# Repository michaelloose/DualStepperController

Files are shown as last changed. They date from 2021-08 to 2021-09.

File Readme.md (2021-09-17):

Stepper Controller
==================

Dieses Projekt entstand als kleines Nebenprojekt im Rahmen meiner Masterarbeit und soll eine performante und einfach anzusteuernde Möglichkeit bieten zwei Schrittmotoren mithilfe eines Schrittmotortreibers wie dem DM542 zu betreiben.

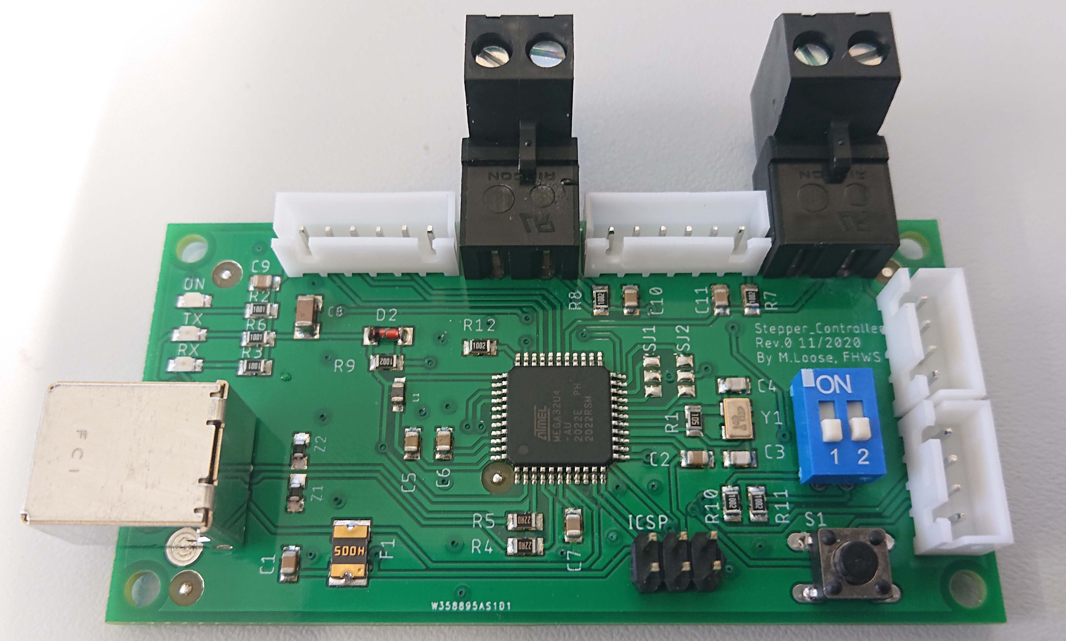
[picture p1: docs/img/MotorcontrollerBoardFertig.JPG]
Platine
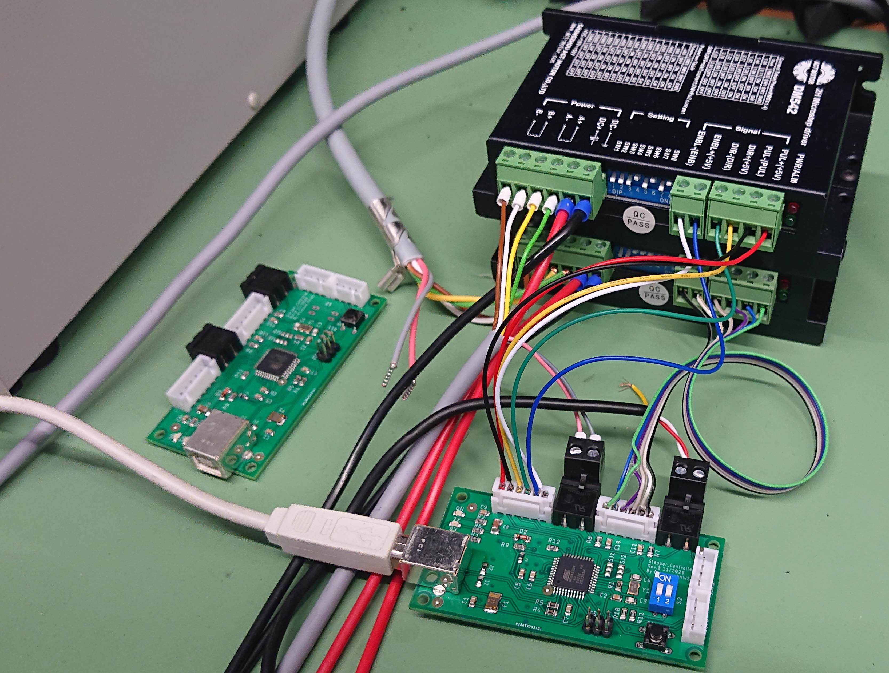
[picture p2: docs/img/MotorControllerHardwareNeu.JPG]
Beispielaufbau
||
|:---:|:---:
|Bestückte Leiterplatte |Beispielhafter Aufbau 

## Befehlsübersicht

Die Übertragung findet
über einen mittels USB-CDC emulierten COM-Port statt. Aus diesem
Grund sind sämtliche Einstellungen zu Baudrate, Daten/Stopbits oder
Paritätsbits hinfällig. Der Controller unterscheidet bei den Befehlen
nicht zwischen Groß- und Kleinschreibung. Das Ende eines Befehles wird
durch ein Carriage Return `<CR> Hex:0x0D` signalisiert. Alternativ wird
auch ein Line Feed `<LF> Hex:0x0A` akzeptiert. Ein Befehl darf eine
maximale Länge von zwölf ASCII-Zeichen zuzüglich des Terminatorzeichens
aufweisen. Wird diese Länge überschritten, so wird das dreizehnte
Zeichen unabhängig vom Inhalt aus Terminator gewertet.\
Zum Testen des Controllers wird eine serielle Konsole benötigt. Dazu
eignet sich die Software *hTerm*, welche sowohl unter Windows
als auch unter Linux ausgeführt werden kann. Um den Motortreiber in eine
Softwareumgebung einzubinden, wurde eine
Treiberklasse in Python entwickelt, die es einem ermöglicht
Steuerbefehle auf einem hohen Level zu senden. Zusätzlich zu dieser
Treiberklasse existiert ebenfalls eine GUI um die Antriebe komfortabel manuell
verfahren zu können.

### Allgemeine Befehle

  |Name               |Befehl     |Erklärung
  |-------------------|-----------|-----------------------------------------------------------------------------------------------------------------------------------------------------
  |Reset              |`RST<cr>`  |Neustart des Controllers. Trennt ebenfalls die USB-Verbindung.
  |Halt               |`HLT<cr>`  |Anhalten aller Antriebe. Neue Befehle werden akzeptiert, Spulen sind weiterhin bestromt.
  |Not-Halt           |`EST<cr>`  |Anhalten aller Antriebe. Neue Befehle werden nicht mehr akzeptiert, Spulenstrom wird abgeschaltet, somit können die Antriebe von Hand bewegt werden
  |Freigabe Not-Halt  |`ESR<cr>`  |Rücksetzen des Not-Halt Zustandes. Spulenstrom wird aktiviert und neue Befehle akzeptiert.

### Steuerbefehle

#### Steuerbefehle an den Controller
 | Byte    |Erlaubte Werte                                | Erklärung
 | ------- |----------------------------------------------| -------------------------------------------------
 | 1       |`A` Antrieb A (Hier Drehtisch)                | Antrieb
 |         |`B` Antrieb B (Hier Linearantrieb)            | 
 | 2       |`P` Position                                  | Art des Befehls
 |         |`S` Geschwindigkeit                           | 
 |         |`H` Anhalten (Setzt Sollwert gleich Istwert)  | 
 |         |`Z` Soll- und Istwert auf 0 setzen            | 
 |         |`R` Referenzfahrt                             | 
 | 3       |`=` Zuweisung                                 | Zuweisung oder Abfrage
 |         |`?` Abfrage                                   | 
 | 4\...   |`<Wert>` Punkt als Dezimalseparator           | Nur für Setzen von Position und Geschwindigkeit
 | N       |`<CR>` Carriage Return                        | Ende eines Befehls

#### Antwort vom Controller

  |Byte   |Erlaubte Werte                             |Erklärung
  |-------|-------------------------------------------|-------------------------------------
  |1..2   |Byte 1 u. 2 des Befehls                    |Wiederholen des empfangenen Befehls
  |3      |`!` Ausführung Abgeschlossen               |Art der Antwort
  |       |`=` Befehl Empfangen, Antwort auf Anfrage  |
  |4\...  |`<Wert>` Punkt als Dezimalseparator        |Wert als Antwort einer Anfrage
  |N      |`<CR>` Carriage Return                     |Ende eines Befehls

### Parametrierbefehle

Um den Controller zu parametrieren muss dieser zunächst mittels des
Befehls `PARAM` in den Parametriermodus gebracht werden. Der Controller
quittiert diesen Modus mit der Ausgabe `PARAM`. In diesem Modus können
die Antriebe nicht verfahren werden. Wird dennoch ein Verfahrbefehl
gesendet, so wird dieser nicht ausgeführt und der Controller antwortet
wie bei einem ungültigen Befehl mit `?`. Der Parametriermodus kann mit
dem Befehl `EXIT` wieder beendet werden. Das Verlassen der
Parametriermodus wird vom Controller mit `OK` Quittiert. Der Controller antwortet auf
Parametrierbefehle in der selben Weise wie auf Steuerbefehle.\

  |Byte    |Erlaubte Werte                          | Erklärung
  |--------|----------------------------------------| ------------------------------------
  |1       |`A` Antrieb A                           | Antrieb
  |        |`B` Antrieb B                           |
  |2\...4  |`SPU`                                   | Schritte pro Einheit
  |        |`VLM`                                   | Geschwindigkeitsbegrenzung \[1,0\]
  |        |`VMX`                                   | Maximale Geschwindigkeit
  |        |`VDF`                                   | Standardgeschwindigkeit
  |        |`PLM`                                   | Positionssbegrenzung \[1,0\]
  |        |`PMX`                                   | Maximale Position
  |        |`PMN`                                   | Minimale Position
  |        |`ROF`                                   | Offset vom Referenzpunkt
  |        |`DIN`                                   | Richtungsumkehrung \[1,0\]
  |        |`RPL`                                   | Polarität Referenzschalter \[1,0\]
  |        |                                        | 0: Öffner, 1: Schließer
  |5       |`=` Zuweisung                           | Zuweisung oder Abfrage
  |        |`?` Abfrage                             | 
  |6\...   |**\<Wert>** Punkt als Dezimalseparator  | 
  |N       |**\<CR>** Carriage Return               | Ende eines Befehls

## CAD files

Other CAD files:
PCB/Partslist.prt

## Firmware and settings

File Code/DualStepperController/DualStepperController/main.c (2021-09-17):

/*
* main.c
*
* Created: 6/11/2021 10:40:07 AM
*  Author: Waxrek
*/
#include "headers.h"





static RingBuffer_t RxBuffer;
static uint8_t RxBufferData[RX_BUFFER_LEN];


/** LUFA CDC Class driver interface configuration and state information. This structure is
*  passed to all CDC Class driver functions, so that multiple instances of the same class
*  within a device can be differentiated from one another.
*/
USB_ClassInfo_CDC_Device_t VirtualSerial_CDC_Interface =
{
	.Config =
	{
		.ControlInterfaceNumber   = INTERFACE_ID_CDC_CCI,
		.DataINEndpoint           =
		{
			.Address          = CDC_TX_EPADDR,
			.Size             = CDC_TXRX_EPSIZE,
			.Banks            = 1,
		},
		.DataOUTEndpoint =
		{
			.Address          = CDC_RX_EPADDR,
			.Size             = CDC_TXRX_EPSIZE,
			.Banks            = 1,
		},
		.NotificationEndpoint =
		{
			.Address          = CDC_NOTIFICATION_EPADDR,
			.Size             = CDC_NOTIFICATION_EPSIZE,
			.Banks            = 1,
		},
	},
};



int main (void) {


	testCounter = 0;
	driveState = DRV_STATE_RDY;
	
	/* Disable watchdog if enabled by bootloader/fuses */
	MCUSR &= ~(1 << WDRF);
	wdt_disable();
	
	/* Disable clock division */
	clock_prescale_set(clock_div_1);
	USB_Init();

	sei();
	
	
	DDRB |= (1 << 0);
	DDRD |= (1 << 5);
	
	PORTB |= (1<<0);    //Bit setzen, LED AUS
	PORTD |= (1<<5);    //Bit setzen, LED AUS
	//PORTD &= ~(1<<5);    //Bit setzen, LED AN
	
	// Initialize the buffer with the created storage array
	RingBuffer_InitBuffer(&RxBuffer, RxBufferData, RX_BUFFER_LEN);
	
	stepper_a_init();
	stepper_b_init();

	while(1){

		/*
		testCounter++;
		
		if(testCounter > 20000){
			testCounter = 0;
			PORTB |= (1<<0);    //Bit setzen, LED AUS
			PORTD &= ~(1<<5);    //Bit loeschen, LED AN
		}
		
		else if(testCounter > 10000){
			// halbe sekunde warten
			PORTB &= ~(1<<0);   // Bit loeschen, LED AN
			PORTD |= (1<<5);    //Bit setzen, LED AUS
		}
		//fputs((char*)&testCounter, &USBSerialStream);
		*/
		
		
		stepper_a_loop(&VirtualSerial_CDC_Interface);
		stepper_b_loop(&VirtualSerial_CDC_Interface);

		putCDCtoBuffer(&VirtualSerial_CDC_Interface, &RxBuffer);
		checkBufferForCommands(&VirtualSerial_CDC_Interface, &RxBuffer);
		
		/*
		if(commandState == CMD_STATE_RDY_TO_EXEC){
			pCommandBuffer = commandBuffer;
			char nextChar = *pCommandBuffer++;
			
			while(nextChar != 0x00){
				CDC_Device_SendByte(&VirtualSerial_CDC_Interface, nextChar);
				nextChar = *pCommandBuffer++;
			}
			commandState = CMD_STATE_EXECUTED;
		}
		*/
		
		handleCommands(&VirtualSerial_CDC_Interface);
		CDC_Device_USBTask(&VirtualSerial_CDC_Interface);
		USB_USBTask();
	}
	
	return 0;
}






/** Event handler for the library USB Connection event. */
void EVENT_USB_Device_Connect(void)
{
	//LEDs_SetAllLEDs(LEDMASK_USB_ENUMERATING);
}

/** Event handler for the library USB Disconnection event. */
void EVENT_USB_Device_Disconnect(void)
{
	//LEDs_SetAllLEDs(LEDMASK_USB_NOTREADY);
}

/** Event handler for the library USB Configuration Changed event. */
void EVENT_USB_Device_ConfigurationChanged(void)
{
	bool ConfigSuccess = true;

	ConfigSuccess &= CDC_Device_ConfigureEndpoints(&VirtualSerial_CDC_Interface);

	//LEDs_SetAllLEDs(ConfigSuccess ? LEDMASK_USB_READY : LEDMASK_USB_ERROR);
}


/** Event handler for the library USB Control Request reception event. */
void EVENT_USB_Device_ControlRequest(void)
{
	CDC_Device_ProcessControlRequest(&VirtualSerial_CDC_Interface);
}

/** CDC class driver callback function the processing of changes to the virtual
*  control lines sent from the host..
*
*  \param[in] CDCInterfaceInfo  Pointer to the CDC class interface configuration structure being referenced
*/
void EVENT_CDC_Device_ControLineStateChanged(USB_ClassInfo_CDC_Device_t *const CDCInterfaceInfo)
{
	/* You can get changes to the virtual CDC lines in this callback; a common
	use-case is to use the Data Terminal Ready (DTR) flag to enable and
	disable CDC communications in your application when set to avoid the
	application blocking while waiting for a host to become ready and read
	in the pending data from the USB endpoints.
	*/
	//bool HostReady = (CDCInterfaceInfo->State.ControlLineStates.HostToDevice & CDC_CONTROL_LINE_OUT_DTR) != 0;
}

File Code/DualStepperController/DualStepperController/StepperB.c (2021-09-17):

/*
* StepperA.c
*
* Created: 05.07.2021 11:06:45
*  Author: Waxrek
*/
//#include "StepperB.h"
#include "headers.h"



void stepper_b_init(){
	
	
	eeprom_read_block(&stepper_b_settings, (void*)STEPPER_B_SETTINGS_START_ADDR, sizeof(stepper_b_settings));
	stepper_b_moving = 0;
	stepper_b_direction = 0;
	stepper_b_hasPreviouslyMoved = 0;
	stepper_b_hasPreviouslyHomed = 0;
	stepper_b_referencing = 0;
	stepper_a_prescalerFactor = 0;
	stepper_b_setpoint = 0;
	stepper_b_position = 0;

	
	
	//Ausgänge definieren
	STEPPER_B_STEP_DDR |= (1 << STEPPER_B_STEP_N);
	STEPPER_B_DIRECTION_DDR |= (1 << STEPPER_B_DIRECTION_N);
	STEPPER_B_ENABLE_DDR |= (1 << STEPPER_B_ENABLE_N);
	//Eingang definieren
	STEPPER_B_REFERENCE_DDR &= ~(1 << STEPPER_B_REFERENCE_N);
	
	//Enable auf HIGH setzen
	STEPPER_B_ENABLE_PORT &= ~(1<<STEPPER_B_ENABLE_N);
	
	//Register fuer Timer setzen
	//Interrupts deaktivieren
	cli();
	// Register mit 0 initialisieren

	STEPPER_B_TIMER_TCCRA = 0b00000000; //Register für PWM
	STEPPER_B_TIMER_TCCRB = 0b00011000;//Register für Prescaler: //WGM12 setzen, WGM13 setzen. Aus Irgend einem Grund Behebt das Setzen von WGM13 das Problem, dass nur das Low Byte vom OCRA Register beschrieben wird
	STEPPER_B_TIMER_TCNT = 0b00000000; //Counter Register
	STEPPER_B_TIMER_TIMSK = 0b00000010;

	sei();
	stepper_b_setSpeed(stepper_b_settings.speed_default);
}


void stepper_b_loop(USB_ClassInfo_CDC_Device_t* pInterface){
// 	if (stepper_b_settings.polarity_reference_switch != ((STEPPER_B_REFERENCE_PIN & (1 << STEPPER_B_REFERENCE_N)) == (1 << STEPPER_B_REFERENCE_N)))
// 	PORTD &= ~(1<<5);    //Bit setzen, LED AN
// 	else
// 	PORTD |= (1<<5);    //Bit setzen, LED AUS
	
	//In welchem Zustand befindet sich der Referenzierungsvorgang?
	switch (stepper_b_referencing)
	{
		case 1:
		//Antrieb bei aufgerufener Referenzierung ausserhalb des Fangbereiches des Endschalters
		
		//Überprüfe ob Istwert = Sollwert
		if(stepper_b_position != stepper_b_setpoint){
			stepper_b_setMotionState((stepper_b_position < stepper_b_setpoint)? 1: -1);
		}
		else{
			stepper_b_setMotionState(0);
			stepper_b_referencing = 0;
		}


		break;
		
		case 2:
		//Antrieb bei aufgerufener Referenzierung ausserhalb des Fangbereiches des Endschalters
		if (stepper_b_settings.polarity_reference_switch != ((STEPPER_B_REFERENCE_PIN & (1 << STEPPER_B_REFERENCE_N)) == (1 << STEPPER_B_REFERENCE_N)))
		{
			
			stepper_b_referencing = 1;

			stepper_b_position = stepper_b_settings.reference_offset * stepper_b_settings.steps_per_unit;
			stepper_b_setpoint = 0;
			
		}
		else
		{
			stepper_b_setMotionState(-1);
		}
		break;

		case 3:
		//Befand sich der antrieb bei aufgerufener Referenzierung im Fangbereich des Endschalters?
		//Ist der Endschalter noch aktiv?
		if (stepper_b_settings.polarity_reference_switch != ((STEPPER_B_REFERENCE_PIN & (1 << STEPPER_B_REFERENCE_N)) == (1 << STEPPER_B_REFERENCE_N)))
		{
			stepper_b_setMotionState(1);
		}
		else
		{
			stepper_b_setMotionState(0);
			stepper_b_referencing = 2;

		}
		break;

		default:
		//Überprüfe ob Istwert = Sollwert
		if(stepper_b_position != stepper_b_setpoint){
			stepper_b_setMotionState((stepper_b_position < stepper_b_setpoint)? 1: -1);
		}
		else{
			stepper_b_setMotionState(0);
		}
		break;
	}

	if ((stepper_b_moving == 0) && (stepper_b_hasPreviouslyMoved == 1))
	{
		

		if (stepper_b_hasPreviouslyHomed && !stepper_b_referencing)
		{
			stepper_b_hasPreviouslyMoved = 0;
			stepper_b_hasPreviouslyHomed = 0;
			CDC_Device_SendString(pInterface, "BR!\r");
		}
		else if(!stepper_b_hasPreviouslyHomed)
		{
			stepper_b_hasPreviouslyMoved = 0;
			CDC_Device_SendString(pInterface, "BP!\r");
		}
	}
	
}

void stepper_b_home(){
	stepper_b_hasPreviouslyMoved = 1;
	stepper_b_hasPreviouslyHomed = 1;

	if (stepper_b_settings.polarity_reference_switch != ((STEPPER_B_REFERENCE_PIN & (1 << STEPPER_B_REFERENCE_N)) == (1 << STEPPER_B_REFERENCE_N)))
	{
		//Status2: Antrieb befindet sich im Fangbereich des Endschalters
		stepper_b_referencing = 3;
		
		
		
	}

	else{
		//Status 1: Antrieb befindet sich nicht im Fangbereich des Endschalters
		stepper_b_referencing = 2;
		
	}
}
void stepper_b_zero(){
	stepper_b_setpoint = 0;
	stepper_b_position = 0;
}

void stepper_b_halt(){
	stepper_b_referencing = 0;
	stepper_b_setpoint = stepper_b_position;
}

uint8_t stepper_b_setSetPoint(double value){
	//Prüfen ob Wert in erlaubtem Bereich falls Positionsbegrenzung aktiviert
	if(stepper_b_settings.position_limit_enabled && ((value > stepper_b_settings.position_max)||(value < stepper_b_settings.position_min)))
	return 1;
	else
	{
		stepper_b_hasPreviouslyMoved = 1;
		stepper_b_setpoint = value * stepper_b_settings.steps_per_unit;
	}
	
	return 0;
}

double stepper_b_getPosition(){
	return (double)stepper_b_position / stepper_b_settings.steps_per_unit;
}


uint8_t stepper_b_setSpeed(double value){
	//Befehl nur akzeptieren wenn Wer
	if (value > 0 && ((value <= stepper_b_settings.speed_max)||stepper_b_settings.speed_max_enabled))
	{

		if ((value * stepper_b_settings.steps_per_unit) > 245)
		{
			//No Prescaler
			stepper_b_prescalerFactor = 1;
		}
		else if ((value * stepper_b_settings.steps_per_unit) > 31)
		{
			//Prescaler=8
			stepper_b_prescalerFactor = 8;
		}
		//Die Fälle ab hier sind eigentlich uninteressant, da sich das Teil eh nie so langsam bewegen wird, aber der Vollständigkeit halber nehm ichs mal auf
		else if ((value * stepper_b_settings.steps_per_unit) > 4)
		{
			//Prescaler=64
			stepper_b_prescalerFactor = 64;
		}
		else
		{
			//Prescaler=256
			stepper_b_prescalerFactor = 256;
		}

		stepper_b_speed_factor = (double)F_CPU / ((double)stepper_b_settings.steps_per_unit * (double)stepper_b_prescalerFactor);
		//Subtracting the Length of one Output Pulse (~2.9us per Step) in TimerRegister Units: Used to compensate the Length of the Pulse, so the Speed is accurate
		
		uint16_t ocr = (uint16_t)((stepper_b_speed_factor / value)-((double)PULSE_LEN * ((double)F_CPU / (double)stepper_b_prescalerFactor)));
		//uint16_t ocr = (uint16_t)(stepper_b_speed_factor / value);

		//_SFR_MEM16(OCRA) = (uint16_t)ocr;
		//Disable Interrupts
		cli();
		//_SFR_MEM8(OCRA+1) = (uint8_t)(ocr>>8);
		//_SFR_MEM8(OCRA) = (uint8_t)ocr;
		STEPPER_B_TIMER_TCNT = 0;
		STEPPER_B_TIMER_OCRA = ocr;
		//Enable Interrupts
		sei();

		return 0;
	}
	else
	{
		return 1;
	}
	
}
double stepper_b_getSpeed(){
	//return (stepper_b_speed_factor / (double)STEPPER_B_TIMER_OCRA);

	return (stepper_b_speed_factor/((double)STEPPER_B_TIMER_OCRA + ((double)PULSE_LEN * ((double)F_CPU / (double)stepper_b_prescalerFactor))));
}
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

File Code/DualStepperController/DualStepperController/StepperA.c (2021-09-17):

/*
* StepperA.c
*
* Created: 05.07.2021 11:06:45
*  Author: Waxrek
*/

#include "headers.h"



void stepper_a_init(){
	
	
	eeprom_read_block(&stepper_a_settings, (void*)STEPPER_A_SETTINGS_START_ADDR, sizeof(stepper_a_settings));
	stepper_a_moving = 0;
	stepper_a_direction = 0;
	stepper_a_hasPreviouslyMoved = 0;
	stepper_a_hasPreviouslyHomed = 0;
	stepper_a_referencing = 0;
	stepper_a_prescalerFactor = 0;
	stepper_a_setpoint = 0;
	stepper_a_position = 0;

	
	
	//Ausgänge definieren
	STEPPER_A_STEP_DDR |= (1 << STEPPER_A_STEP_N);
	STEPPER_A_DIRECTION_DDR |= (1 << STEPPER_A_DIRECTION_N);
	STEPPER_A_ENABLE_DDR |= (1 << STEPPER_A_ENABLE_N);
	//Eingang definieren
	STEPPER_A_REFERENCE_DDR &= ~(1 << STEPPER_A_REFERENCE_N);
	
	//Enable auf HIGH setzen
	STEPPER_A_ENABLE_PORT &= ~(1<<STEPPER_A_ENABLE_N);
	
	//Register fuer Timer setzen
	//Interrupts deaktivieren
	cli();
	// Register mit 0 initialisieren

	STEPPER_A_TIMER_TCCRA = 0b00000000; //Register für PWM
	STEPPER_A_TIMER_TCCRB = 0b00011000;//Register für Prescaler: //WGM12 setzen, WGM13 setzen. Aus Irgend einem Grund Behebt das Setzen von WGM13 das Problem, dass nur das Low Byte vom OCRA Register beschrieben wird
	STEPPER_A_TIMER_TCNT = 0b00000000; //Counter Register
	STEPPER_A_TIMER_TIMSK = 0b00000010;

	sei();
	stepper_a_setSpeed(stepper_a_settings.speed_default);
}

void stepper_a_loop(USB_ClassInfo_CDC_Device_t* pInterface){
	// 	if (stepper_a_settings.polarity_reference_switch != ((STEPPER_A_REFERENCE_PIN & (1 << STEPPER_A_REFERENCE_N)) == (1 << STEPPER_A_REFERENCE_N)))
	// 	PORTD &= ~(1<<5);    //Bit setzen, LED AN
	//
	// 	else
	// 	PORTD |= (1<<5);    //Bit setzen, LED AUS
	
	//In welchem Zustand befindet sich der Referenzierungsvorgang?
	switch (stepper_a_referencing)
	{
		case 1:
		//Antrieb bei aufgerufener Referenzierung ausserhalb des Fangbereiches des Endschalters
		
		//Überprüfe ob Istwert = Sollwert
		if(stepper_a_position != stepper_a_setpoint){
			stepper_a_setMotionState((stepper_a_position < stepper_a_setpoint)? 1: -1);
		}
		else{
			stepper_a_setMotionState(0);
			stepper_a_referencing = 0;
		}


		break;
		
		case 2:
		//Antrieb bei aufgerufener Referenzierung ausserhalb des Fangbereiches des Endschalters
		if (stepper_a_settings.polarity_reference_switch != ((STEPPER_A_REFERENCE_PIN & (1 << STEPPER_A_REFERENCE_N)) == (1 << STEPPER_A_REFERENCE_N)))
		{
			
			stepper_a_referencing = 1;

			stepper_a_position = stepper_a_settings.reference_offset * stepper_a_settings.steps_per_unit;
			stepper_a_setpoint = 0;
			
		}
		else
		{
			stepper_a_setMotionState(-1);
		}
		break;

		case 3:
		//Befand sich der antrieb bei aufgerufener Referenzierung im Fangbereich des Endschalters?
		//Ist der Endschalter noch aktiv?
		if (stepper_a_settings.polarity_reference_switch != ((STEPPER_A_REFERENCE_PIN & (1 << STEPPER_A_REFERENCE_N)) == (1 << STEPPER_A_REFERENCE_N)))
		{
			stepper_a_setMotionState(1);
		}
		else
		{
			stepper_a_setMotionState(0);
			stepper_a_referencing = 2;

		}
		break;

		default:
		//Überprüfe ob Istwert = Sollwert
		if(stepper_a_position != stepper_a_setpoint){
			stepper_a_setMotionState((stepper_a_position < stepper_a_setpoint)? 1: -1);
		}
		else{
			stepper_a_setMotionState(0);
		}
		break;
	}

	if ((stepper_a_moving == 0) && (stepper_a_hasPreviouslyMoved == 1))
	{
		

		if (stepper_a_hasPreviouslyHomed && !stepper_a_referencing)
		{
			stepper_a_hasPreviouslyMoved = 0;
			stepper_a_hasPreviouslyHomed = 0;
			CDC_Device_SendString(pInterface, "AR!\r");
		}
		else if(!stepper_a_hasPreviouslyHomed)
		{
			stepper_a_hasPreviouslyMoved = 0;
			CDC_Device_SendString(pInterface, "AP!\r");
		}
	}
	
}

void stepper_a_home(){
	stepper_a_hasPreviouslyMoved = 1;
	stepper_a_hasPreviouslyHomed = 1;

	if (stepper_a_settings.polarity_reference_switch != ((STEPPER_A_REFERENCE_PIN & (1 << STEPPER_A_REFERENCE_N)) == (1 << STEPPER_A_REFERENCE_N)))
	{
		//Status2: Antrieb befindet sich im Fangbereich des Endschalters
		stepper_a_referencing = 3;
		
		
		
	}

	else{
		//Status 1: Antrieb befindet sich nicht im Fangbereich des Endschalters
		stepper_a_referencing = 2;
		
	}
}
void stepper_a_zero(){
	stepper_a_setpoint = 0;
	stepper_a_position = 0;
}

void stepper_a_halt(){
	stepper_a_referencing = 0;
	stepper_a_setpoint = stepper_a_position;
}

uint8_t stepper_a_setSetPoint(double value){
	//Prüfen ob Wert in erlaubtem Bereich falls Positionsbegrenzung aktiviert
	if(stepper_a_settings.position_limit_enabled && ((value > stepper_a_settings.position_max)||(value < stepper_a_settings.position_min)))
	return 1;
	else
	{
		stepper_a_hasPreviouslyMoved = 1;
		stepper_a_setpoint = value * stepper_a_settings.steps_per_unit;
	}
	
	return 0;
}

double stepper_a_getPosition()
{
	return (double)stepper_a_position / stepper_a_settings.steps_per_unit;
}


uint8_t stepper_a_setSpeed(double value){
	//Befehl nur akzeptieren wenn Wer
	if (value > 0 && ((value <= stepper_a_settings.speed_max)||stepper_a_settings.speed_max_enabled))
	{

		if ((value * stepper_a_settings.steps_per_unit) > 245)
		{
			//No Prescaler
			stepper_a_prescalerFactor = 1;
		}
		else if ((value * stepper_a_settings.steps_per_unit) > 31)
		{
			//Prescaler=8
			stepper_a_prescalerFactor = 8;
		}
		//Die Fälle ab hier sind eigentlich uninteressant, da sich das Teil eh nie so langsam bewegen wird, aber der Vollständigkeit halber nehm ichs mal auf
		else if ((value * stepper_a_settings.steps_per_unit) > 4)
		{
			//Prescaler=64
			stepper_a_prescalerFactor = 64;
		}
		else
		{
			//Prescaler=256
			stepper_a_prescalerFactor = 256;
		}
		
		stepper_a_speed_factor = (double)F_CPU / ((double)stepper_a_settings.steps_per_unit * (double)stepper_a_prescalerFactor);
		//Subtracting the Length of one Output Pulse (~2.9us per Step) in TimerRegister Units: Used to compensate the Length of the Pulse, so the Speed is accurate
		
		//uint16_t ocr = (uint16_t)(stepper_a_speed_factor / value);
		uint16_t ocr = (uint16_t)((stepper_a_speed_factor / value)-((double)PULSE_LEN * ((double)F_CPU / (double)stepper_a_prescalerFactor)));


		//_SFR_MEM16(OCRA) = (uint16_t)ocr;
		//Disable Interrupts
		cli();
		//_SFR_MEM8(OCRA+1) = (uint8_t)(ocr>>8);
		//_SFR_MEM8(OCRA) = (uint8_t)ocr;
		STEPPER_A_TIMER_TCNT = 0;
		STEPPER_A_TIMER_OCRA = ocr;
		//Enable Interrupts
		sei();

		return 0;
	}
	else
	{
		return 1;
	}
	
}
double stepper_a_getSpeed(){
	return (stepper_a_speed_factor/((double)STEPPER_A_TIMER_OCRA + ((double)PULSE_LEN * ((double)F_CPU / (double)stepper_a_prescalerFactor))));

	//return (stepper_a_speed_factor / (double)STEPPER_A_TIMER_OCRA);
}
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

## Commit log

2020-12-15 Changed Pinmap to fit to new Board
2021-08-03 Fixing Bug with drives not accepting direction inverse commands when in motion
    [StepperA.c, StepperB.c]
